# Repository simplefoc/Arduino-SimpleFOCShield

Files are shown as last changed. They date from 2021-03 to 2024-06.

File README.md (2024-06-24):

# Arduino *Simple**FOC**Shield* *v3.2*

  

This is an open-source low-cost Brushless DC (BLDC) motor driver board intended primarily for low-power FOC applications up to 5Amps. The board is fully compatible with the Arduino UNO and all the boards with the standard Arduino headers. The *Simple**FOC**Shield*, in combination with the *Simple**FOC**library* provides user-friendly way to control BLDC motors both in hardware and software. 

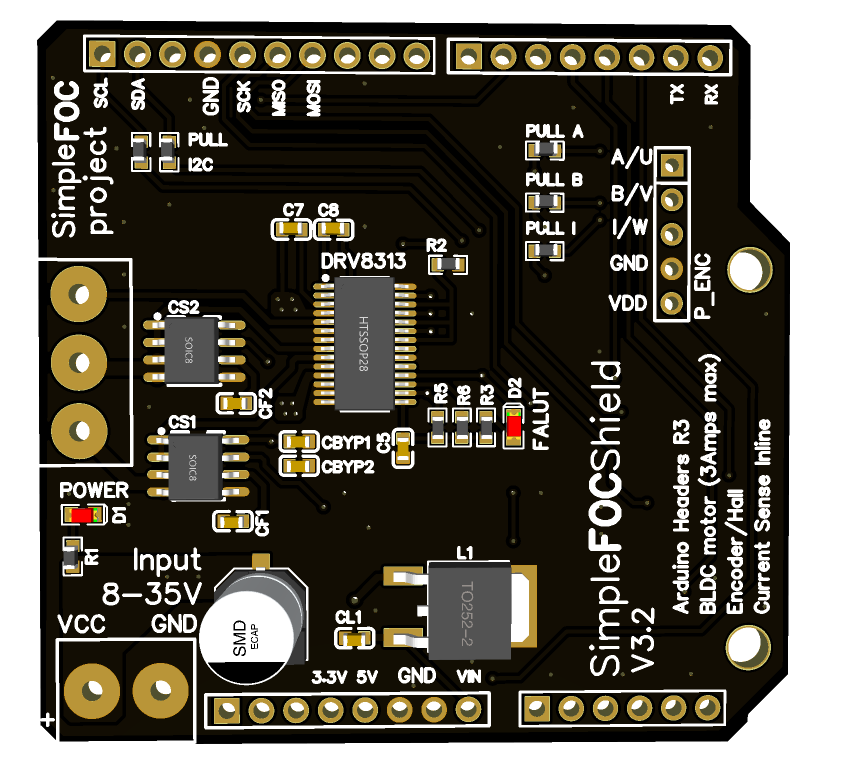
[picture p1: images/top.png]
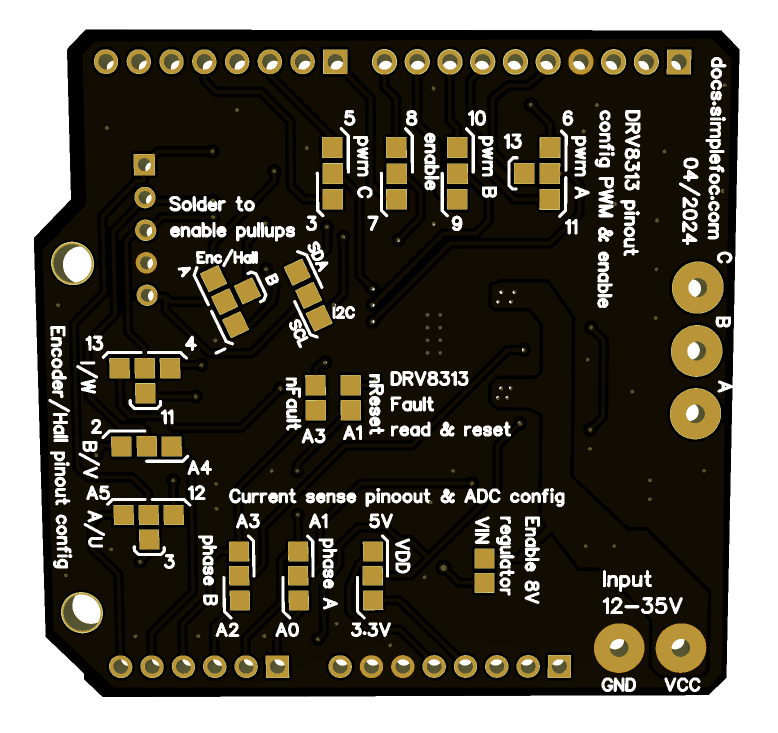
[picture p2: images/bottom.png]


### Features
- **Plug & play**: In combination with Arduino *Simple**FOC**library* - [github](https://github.com/simplefoc/Arduino-FOC)
- **Low-cost**: Price of 15-30€ - [Check the pricing](https://www.simplefoc.com/shop) 
- **In-line current sensing**: Up to 5Amps bidirectional
   - ACS712 hall current sensor
- **Integrated 8V regulator**: 
   - Enable/disable by soldering pads
- **Absolute max ratings** - Designed for Gimbal motors with the internal resistance >10 Ωs. 
   - Max current: 3A, 
   - Max input voltage: 35V
- **Stackable**: running 2 motors in the same time
- **Encoder/Hall sensors interface**: Integrated 3.3kΩ pullups (configurable)
- **I2C interface**: Integrated 4.7kΩ pullups (configurable)
- **Configurable pinout**: Hardware configuration - soldering connections
- **Arduino headers**: Arduino UNO, Arduino MEGA, STM32 Nucleo boards...
- **Open Source**: 
   - Fully designed in **EasyEDA**: [EasyEDA project](https://oshwlab.com/the.skuric/simplefocshield_copy_copy) 🎉
   - Fully available fabrication files - [how to make it yourself](https://docs.simplefoc.com/arduino_simplefoc_shield_fabrication)

### New Features v3.x
 - Transition away from stm's L6234 chip to [DRV8313](https://www.ti.com/lit/ds/symlink/drv8313.pdf?ts=1719079575798), which is much more available
 - Transition form TI's INA240 current amps to Allegro's [ACS712](https://www.sparkfun.com/datasheets/BreakoutBoards/0712.pdf) hall sensors
 - Smaller footprint: 56mm x 53mm
 - Fault and reset pins exposed (optional)
 - Fault led indication
 - Designed completely in EasyEDA, which is a free online PCB design tool - **[Official Easy EDA project](https://oshwlab.com/the.skuric/simplefocshield_copy_copy)**

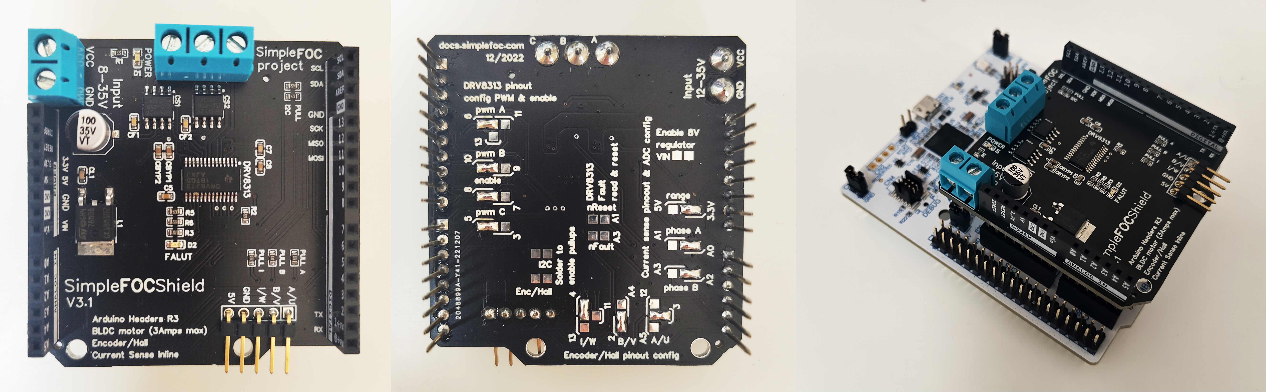
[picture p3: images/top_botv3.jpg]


### Short YouTube demonstration video :D
<p align="">
<a href="https://youtu.be/G5pbo0C6ujE">

</a>
</p>

### Short video guide to fabricating your own *Simple**FOC**Shield* 
<p align="">
<a href="https://youtu.be/sax_9sUgBuk">
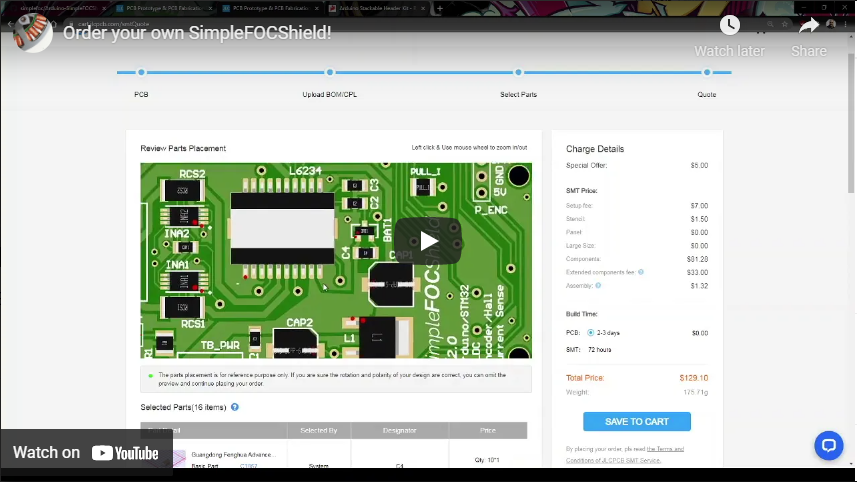
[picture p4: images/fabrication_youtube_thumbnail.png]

</a>
</p>

More info on [board fabrication docs](https://docs.simplefoc.com/arduino_simplefoc_shield_fabrication).

## Board versions:

Feature | <span class="simple">Simple<span class="foc">FOC</span>Shield</span> v1.x | <span class="simple">Simple<span class="foc">FOC</span>Shield</span> v2.x | <span class="simple">Simple<span class="foc">FOC</span>Shield</span> v3.x |
|-|-|-|-|
||||
**PWM Driver** | [L6234](https://www.st.com/resource/en/datasheet/l6234.pdf) | [L6234](https://www.st.com/resource/en/datasheet/l6234.pdf) | [DRV8313](https://www.ti.com/lit/ds/symlink/drv8313.pdf?ts=1719165774986&ref_url=https%253A%252F%252Fwww.google.com%252F)
**Current Sense** | ❌ | [INA240](https://www.ti.com/lit/ds/symlink/ina240.pdf?ts=1719180172738) | [ACS712](https://www.allegromicro.com/en/products/sense/current-sensor-ics/zero-to-fifty-amp-integrated-conductor-sensor-ics/acs712)
**Current measurement range** | ❌ | (configurable) ±3.3/5Amps | ±5Amps
**Onboard LDO** | ❌ | LM7808 | LM7808
**Stackable** | ✔️ | ✔️ | ✔️
**Max current** | 2Amps (5Amp peak) | 2Amps (5Amp peak) | 2Amps (3Amp peak)
**Max voltage** | 24V | 35V | 35V
**Protections** | Overtemperature | Overtemperature | Overtemperature, Overcurrent
**Footprint** | 68mm x 53 mm | 68mm x 53 mm | 56mm x 53mm
**Design tool** | Altium Designer 2019 | Altium Designer 2019 | EasyEDA 

## Release timeline

To check the release timeline, click [here](https://github.com/simplefoc/Arduino-SimpleFOCShield/releases) 

Version  |link | Release date | Comment
----- | ----- | ---- | ----
*Simple**FOC**Shield* v1.3 |[release v1.3](https://github.com/simplefoc/Arduino-SimpleFOCShield/releases/tag/v1.3) | 04/20 | Inital release
*Simple**FOC**Shield* v1.3.1 | [release v1.3.1](https://github.com/simplefoc/Arduino-SimpleFOCShield/releases/tag/v1.3.1) | 07/20 | added Nucleo stacking support
*Simple**FOC**Shield* v1.3.2 |[release v1.3.2](https://github.com/simplefoc/Arduino-SimpleFOCShield/releases/tag/v1.3.2) | 09/20 | added I2C pullups
*Simple**FOC**Shield* v1.3.3 |[release v1.3.3](https://github.com/simplefoc/Arduino-SimpleFOCShield/releases/tag/v1.3.3) | 12/20 | adapted L6234 circuit + full Arduino header
*Simple**FOC**Shield* v2.0 |[release v2.0](https://github.com/simplefoc/Arduino-SimpleFOCShield/releases/tag/v2.0) | 01/21 | - 3A in-line current sensing <br>- 5V regulator <br>- new pinout for hardware config 
*Simple**FOC**Shield* v2.0.1 |[release v2.0.1](https://github.com/simplefoc/Arduino-SimpleFOCShield/releases/tag/v2.0.1) | 01/21 | - reduced via size <br> - configurable range
*Simple**FOC**Shield* v2.0.2 |[release v2.0.2](https://github.com/simplefoc/Arduino-SimpleFOCShield/releases/tag/v2.0.2) | 02/21 | replaced 7805(connected to 5V) with 78M08 (connected to VIN) to be compatible with stm32 Nucleo-64
*Simple**FOC**Shield* v2.0.3 |[release v2.0.3](https://github.com/simplefoc/Arduino-SimpleFOCShield/releases/tag/v2.0.3) | 03/21 | - Shortened the lines from ADC to current sense <br> - Typo fix : underside label switched phase A and phase B
*Simple**FOC**Shield* v2.0.4 |[release v2.0.4](https://github.com/simplefoc/Arduino-SimpleFOCShield/releases/tag/v2.0.4) | 09/21 | - Pullup config simplified <br> - Max input voltage 35V <br> - removed CAP2 for a CL1 <br> - Easy EDA version of the project
*Simple**FOC**Shield* v3.1 |release v3.1 | 10/22 | - Complete redesign <br> - Transition to DRV8313 <br> - Transition to ACS712 <br> - Smaller footprint: 56mm x 53mm<br> - Fault and reset pins exposed (optional) <br> - Fault led indication <br>- Fully developed using EasyEDA
*Simple**FOC**Shield* v3.2 |[release v3.2](https://github.com/simplefoc/Arduino-SimpleFOCShield/releases/tag/v2.0.4) | 04/24 | - Official release <br> - Resolved the bug [#9](https://github.com/simplefoc/Arduino-SimpleFOCShield/issues/9)

## Getting started
You already have your own <span class="simple">Simple<span class="foc">FOC</span>Shield</span>? <br>
[Here is a simple guide how to start preparing your setup](https://docs.simplefoc.com/arduino_simplefoc_shield_installation)

## How to get hold of the *<span class="simple">Simple<span class="foc">FOC</span>Shield</span>*
- **Fabricate the board yourself**:  Please visit the [board fabrication](https://docs.simplefoc.com/arduino_simplefoc_shield_fabrication) to find out how to manufacture the board yourself!<br>
- **Order the finished and tested board**:  Check out our [shop](https://simplefoc.com/simplefoc_shield_product).

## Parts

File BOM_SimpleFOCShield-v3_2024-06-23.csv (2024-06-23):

ID | Name | Designator | Footprint | Quantity | Manufacturer Part | Manufacturer | Supplier | Supplier Part | Price
1 | 470nF | C5 | C0603 | 1 | CC0603ZRY5V6BB474 | YAGEO | LCSC | C327269 | 0.009
2 | 100uF | C6 | CAP-SMD_BD6.3-L6.6-W6.6-FD | 1 | VT1V101M-CRE77 | Vertical Technology | LCSC | C294520 | 0.033
3 | 100nF | C7,C8 | C0603 | 2 | CL10B104KB8NNNC | SAMSUNG | LCSC | C1591 | 0.002
4 | 1uF | CBYP1,CBYP2 | C0603 | 2
5 | 1nF | CF1,CF2 | C0603 | 2
6 | 0.1u | CL1 | C0603 | 1
7 | ACS712ELCTR-05B-T | CS1,CS2 | SOIC-8_L5.0-W4.0-P1.27-LS6.0-BL | 2 | ACS712ELCTR-05B-T | ALLEGRO(美国埃戈罗) | LCSC | C44471 | 1.757
8 | LED-0603_R | D1 | LED0603_RED | 1 | 19-217/R6C-AL1M2VY/3T | EVERLIGHT(台湾亿光) | LCSC | C72044 | 0.018
9 | LED-0603_R | D2 | LED0603_RED | 1 | 19-217/R6C-AL1M2VY/3T | EVERLIGHT(台湾亿光) | Add New Supplier | C72044 | 0.018
10 | DRV8313PWPR | DRV8313 | HTSSOP-28_L9.8-W4.5-P0.65-LS6.6-BL-EP | 1 | DRV8313PWPR | Texas Instruments | LCSC | C92482 | 2.072
11 | L78M08CDT-TR | L1 | TO-252-2_L6.6-W6.1-P4.57-LS9.9-TL-CW | 1 | L78M08CDT-TR | STMicroelectronics | LCSC | C158076 | 0.478
12 | 3.3k | PULL_A1,PULL_I1 | R0603 | 2
13 | 3.3k | PULL_B1 | R0603 | 1 |  |  | LCSC
14 | 4.7k | PULL_SCL,PULL_SDA,R1 | R0603 | 3 | 0603WAF4701T5E | UniOhm | LCSC | C23162 | 0.001
15 | 4.7kΩ | R2,R5,R6 | R0603 | 3 | 0603WAF4701T5E | UniOhm | LCSC | C23162 | 0.001
16 | 330Ω | R3 | R0603 | 1

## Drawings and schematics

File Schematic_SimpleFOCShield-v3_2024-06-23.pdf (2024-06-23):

# ACS712

# Current Sense Circuit

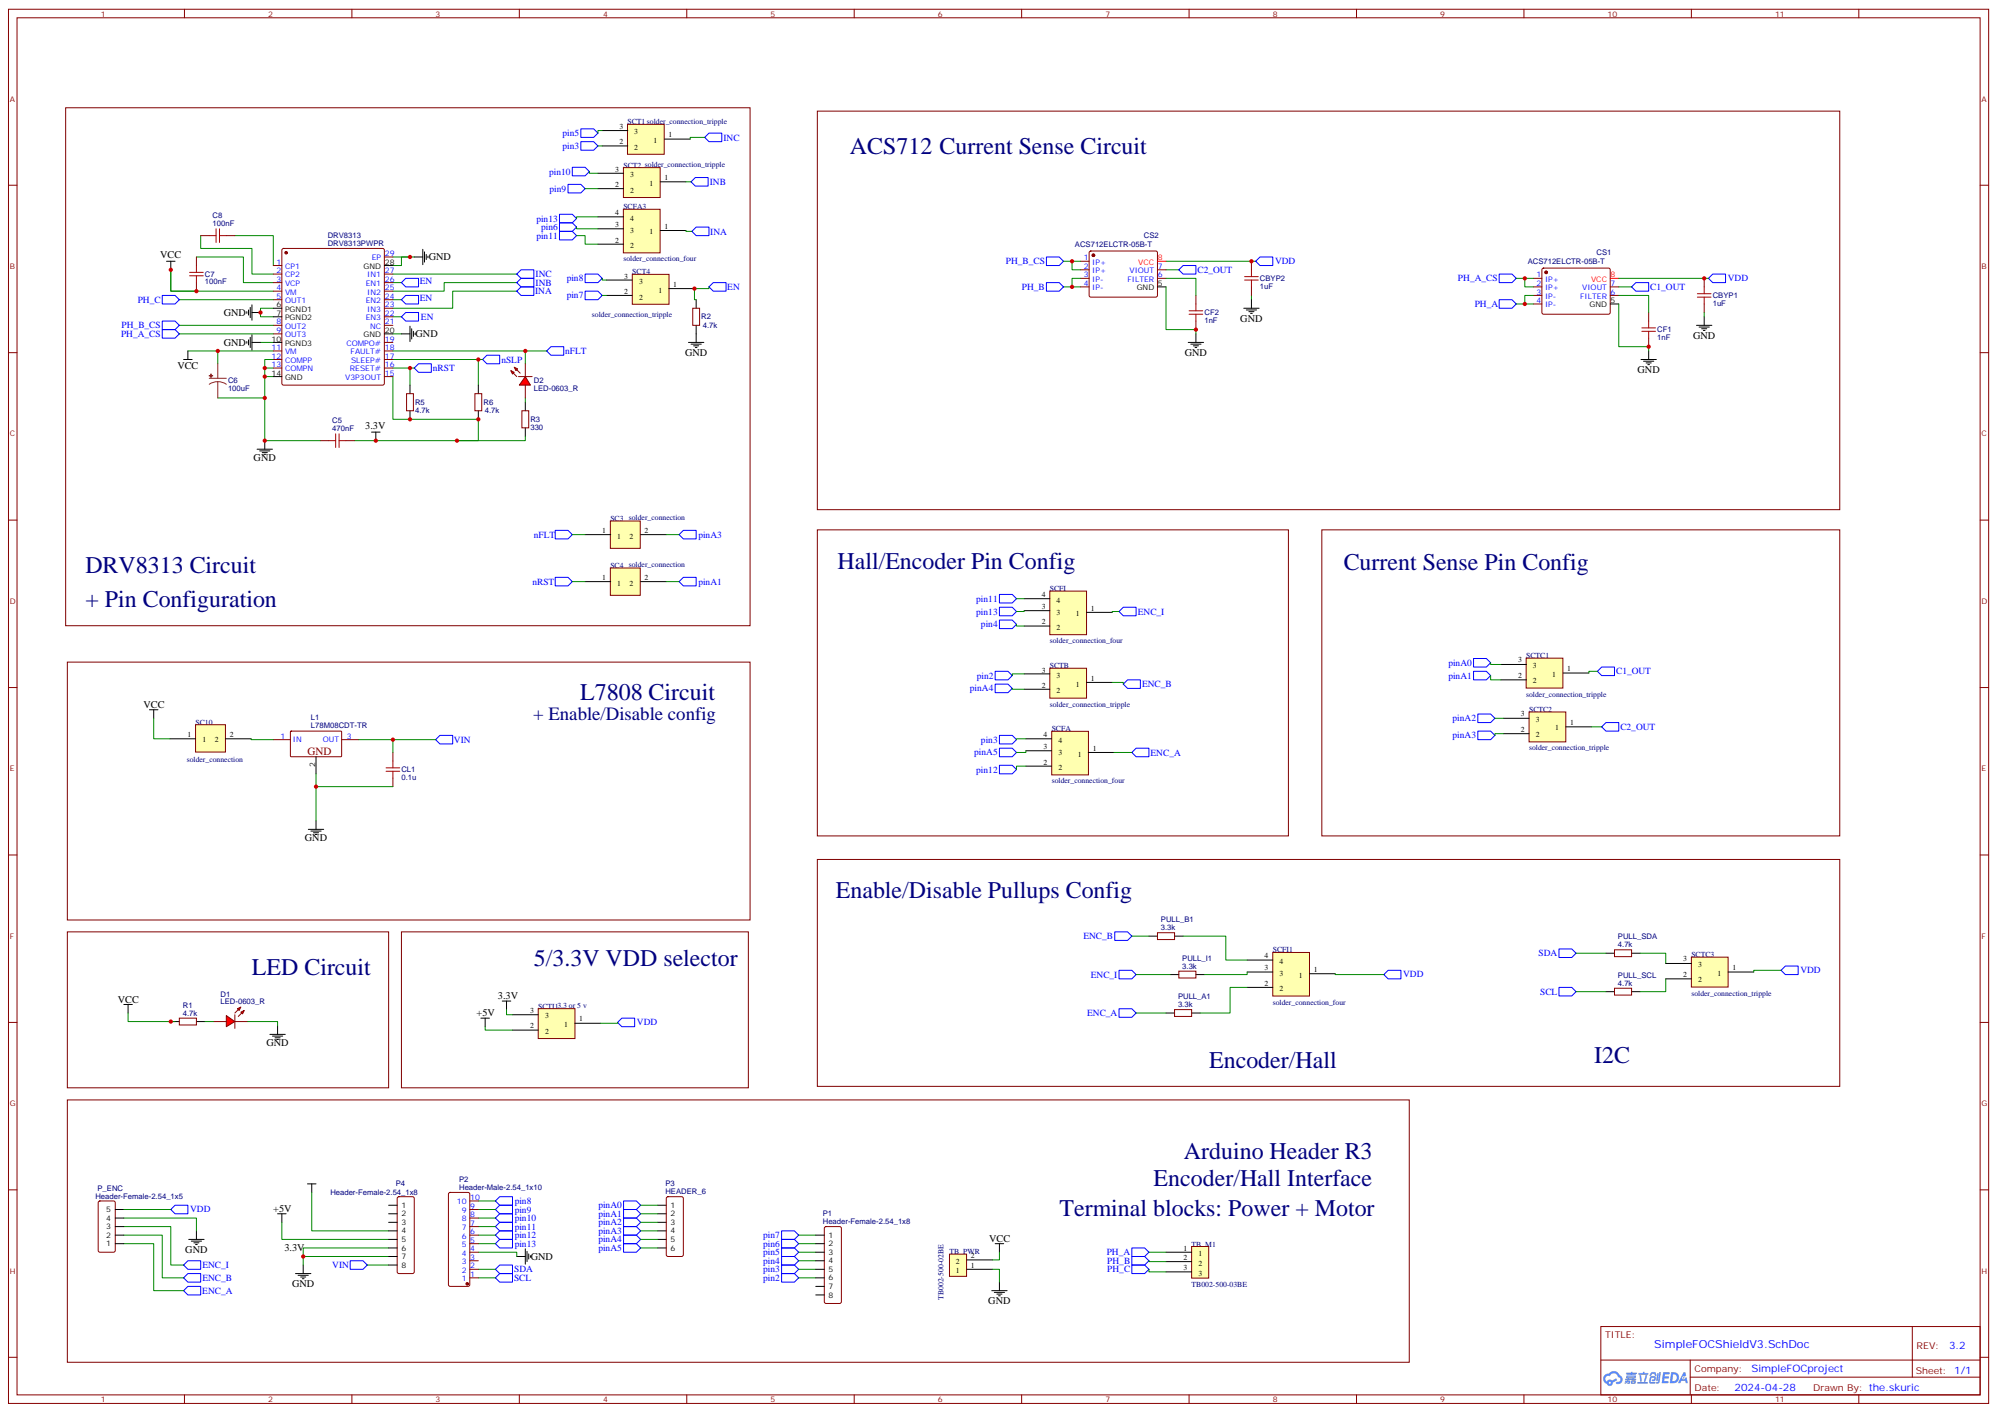
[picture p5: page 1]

Hall/Encoder Pin Config

Current Sense Pin Config

Enable/Disable Pullups Config

Terminal blocks: Power + Motor

Drawn By: the.skuric

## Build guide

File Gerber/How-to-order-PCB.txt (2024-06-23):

How to Order PCB

Please refer to:
https://docs.easyeda.com/en/PCB/Order-PCB

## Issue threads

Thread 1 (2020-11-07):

[Schematic] Diode TBAT45s pin identification error

kingsjl, 2020-11-07:
Schematic diode pin identification error：
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

Correct pin sequence：
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

Closed 2020-11-07.

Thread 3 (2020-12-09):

Arduino SimpleFOCShiled v1.3.3 design error

askuric, 2020-12-09:
Hi guys,

Aaron has just identified a problem with the version of the board v1.3.3.
Check the community forum for more info:
https://community.simplefoc.com/t/motor-makes-loud-noise/316/11

I'll make sure to update the design as soon as possible!

askuric, 2020-12-09:
The v1.3.3 has been fixed to remove the error in [the commit](https://github.com/simplefoc/Arduino-SimpleFOCShield/commit/ead7f148952500506279881f43028458ff9d675f)
The [release v1.3.3](https://github.com/simplefoc/Arduino-SimpleFOCShield/releases/tag/v1.3.3) has been updated to include this bugfix.

Sorry about the inconvenience!

Closed 2021-04-04.

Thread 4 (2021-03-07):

INA240: which gain should be selected for V2.0.2

gowitty, 2021-03-07:
there 4 different gains.  which gain should be selected?
INA240A1 GAIN(V/V) 20
INA240A2 GAIN(V/V) 50
INA240A3 GAIN(V/V) 100
INA240A4 GAIN(V/V) 200

askuric, 2021-03-07:
Hey @gowitty,

So in short, I've taken a choice to use:
- Shunt resistor value: **0.01Ohm**
- Current sense: **INA240A2 (gain 50)**

#### Here is why:

So in general there are two parameters when it comes to current sensing hardware:
 - shunt resistor values
 - amplifier gain

In the case of the *Simple**FOC**Shield*, the BLDC driver chip L6234 has the current limit of 5 Amps. So we need to be able to measure +-5amp current. But in most cases your application with the *Simple**FOC**Shield* will remain in the 3Amp range. Higher currents require appropriate heat evacuation: heat-sinks, fans, etc.

So you need to be able to measure +-3amps for example, which is a 6Amp range.  (or +- 5amps -> 10amp range).
The mcus usually have the 3.3V or 5V logic which tells you that you need the transformation ratiofor example:
```
trans_ratio = 5V / 10amps = 0.5 V/Amp    or    trans_ratio = 3.3V / 10amps = 0.33 V/Amp
```

So now that we know what is the transformation ratio that we need we can proceed to finding the shunt resistor value and the amplification gain. We know that the `trans_ratio = amp_gain*shunt_resistance`. Now there is a trade-off here in between amplification gain and shunt value:
Shunt resistance will be placed in-line with the motor and all the phase current of the motor will pass through the shunt resistor so it is important to choose the value that is the smallest possible value to reduce the heat loss. Additionally by adding the shunt resistors in-line with motors we are actually increasing the phase resistance of the motor, and since we are placing shunt resistors only on two phases this can make the motor unbalanced and this is another reason that makes it really important to keep this value small relatively to the phase resistance of the motor. On the other hand, the smaller the shunt resistor value the smaller the voltage across it that we want to measure. Since the voltage across it is smaller it which makes it more difficult to measure the phase current, because the smaller it is the higher the amplification noise.  So we would prefer to have the shunt resistor value high and amplification gain low to reduce the noise.

Since we know that the phase resistances of the BLDC motors to be used with this board will be in the range of >10Ohm we know that we can take the shunt resistor of >0.01Ohm.
Now we can calculate that for shunt resistor of 0.01 Ohm we would need the amplificaiton gain:
```
amp_gain= 0.5/0.01 = 50     or     amp_gain =  3.3/0.01 = 33
```
So in order to measure the +-5Amps on 5V logic we can use INA240A2 (gain 50)  but on the 3.3V logic that will give us +-3.3Amp range.
If we want to have higer range on 3.3V logic we need to either:
- use INA240A1 (gain 20) which will give us +-8.25Amp range on 3.3V and +-12.5Amp range on 5V.
- use INA250A2 (gain 50) and change the shunt value (ex. 6 miliOhm) which would give use +-5.5Amps range on 3.3V and +-8.5Amps range on 5V

So I've decided to stick with the **0.01Ohm** shunt and **INA240A2** because even +-3.3Amp range is perfectly enough for gimbal motors.

gowitty, 2021-03-13:
Hey @askuric
appreciate sharing so many details!

Closed 2021-03-13.

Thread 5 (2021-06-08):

Header pins too tall?

steph643, 2021-06-08:
On the left, a nucleao-64 with its 8mm pins. On the right, my brand new SimpleFOCShield with its 18.5mm pins, which cannot penetrate fully into the 9mm Arduino header.
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
Is it unintended or am I missing something?

steph643, 2021-08-08:
> I've pivoted from them, for the newest batch though. Even they were out of stock

I'm fighting to find the same kind of connector (in double-row). Would you disclose who your supplier is?

askuric, 2021-08-09:
Hey @steph643,
I've tried many of them and I am buying them online from the webshops as well. Because my quantities are small.

So I've started with the mouser, where I've bought every component separately. But they soon rum out of components.
Then I've bought them from spark fun. But they to run out.
Then Arduino webshop.
The last one I've bought was from afafruit.

And then even the other components disappeared from the market 😃

Closed 2021-06-08.

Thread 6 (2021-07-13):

OneWheel question

vfear, 2021-07-13:
Hello, I am doing a project onewheel, I need a controller with the ability to control the balance.  I have a hoverboard controller with firmware https://github.com/EmanuelFeru/hoverboard-firmware-hack-FOC.  the controller can be controlled via arduino using uart.  can you help me to adapt the balance code with sending to uart.  This is how my project looks like.
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

askuric, 2021-07-20:
Hey @vfear
Very nice project. I have one Onewheel myself and they are relly fun!

I dont think your question has much to do with this repo so I'll transfer it to the balancer repo.

Do you have some kind of IMU or an accelerometer integrated on the board?
Do you use one or two motors for the wheel, in the picture it seems like they are two :D

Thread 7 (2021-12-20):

confuse about pin mux

standback, 2021-12-20:
hi guys.
i have question about  "Customizing pinout",
In the docs.
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
pwmA mapping to pin 9/10
pwmB mapping to pin 3/5

But , according the  note below
`
Now, there is a lot of possible pin configurations and not all of them are possible depending on the microcontroller and sensor you are using. For example, Arduino UNO only has 2 external interrupt pins, and they are pin 2 and 3. Therefore when using the board with Arduino UNO and Encoder we will try to use pin 3 for encoder channel A and not for pwm A.`
it seems mean that  PwmA should  mapping to pin3  instand 9/10.
version2.03 board ,also design that pinA mapping to pin 3/5.
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

is that means  this pinmux(in docs) is  out of date?

I am confused.
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
,
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
which one is right?

askuric, 2021-12-20:
Yeah, it's the docs. It was an example pin out for the earlier version of the board.
Whatever is indicated on the board itself is the right configuration.

We try to keep the docs as up-to-date as possible, but these kinds of stuff are sometimes difficult to detect :)

We'll update it as soon as possible.

standback, 2021-12-20:
Got it,  thanks for your reply.

Closed 2021-12-20.

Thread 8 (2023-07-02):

Increase current limit

kilofeq, 2023-07-02:
Which components I need to change to operate motors with around 10-15A of peak current?

askuric, 2023-07-03:
Hey @kilofeq,

The l6234 driver is not able to drive these kinds of currents.
So you would need a different driver chip, which in most cases is not all in one integrated chip, but would require a set of high and low side mosfets as well as the mosfet driver.
There is no simple way of building on top of the simplefocshiled to achivene thse currents. Its probably easier to start from scratch.

There is a board that might be of interest to you, called [simplefoc-powershield](https://github.com/simplefoc/Arduino-SimpleFOC-PowerShield). with the 30amp current limts, but its performance is relatively limited. Having many issues with the efficiency on higher pwm frequencies.

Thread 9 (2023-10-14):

I2C pullups using ESP32-S2 Metro

wasistdalos, 2023-10-14:
Hi, thank you a lot for the project, the documentation and effort! using the ESP32-S2 Metro there are already I2C pullups included so i didn't connect the jumper on the SimpleFOC V2.0.4. Using that setup with an AS5048b i did run into issues getting I2C communication to work.  Whitout the shield it did work as expected. I solved the issue by desoldering one of the 4,7k I2C pullups of the V2.0.4 shield.  Please check for next shield version, thank you!
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

askuric, 2023-10-14:
Hey @hammerflo,

This is very strange! :thinking:

Did you try to desolder the connection (solder pad) on the bottom side of the board?
There is one:
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

hammerflo, 2023-10-14:
yes i did. looking at the schematic, sda and scl are connected with 2x 4,7k on the shield. maybe this leads to this behaviour?

askuric, 2023-10-14:
Nice catch!
This could be an issue, I did not think about that.
And in that case it make sense that desoldering one of the resistors solved the problem.

I've connected their 5V channel to reduce the number of soldering pads in the v2.0.4. Earlier versions did not have this issue. I'll make sure to separate them in the next release.

askuric, 2024-06-26:
The issue is resolved in the new version of the shield :D

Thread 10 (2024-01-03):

Bad Getting Started link

Candas1, 2024-01-03:
Hi,

It seems the getting started link doesn't work in the readme.
I believe it should be this one:
https://docs.simplefoc.com/arduino_simplefoc_shield_installation

askuric, 2024-06-22:
Thanks I've corrected it!

Closed 2024-06-22.

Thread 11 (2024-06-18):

JLC PCB fabrication instructions no longer work

eduardkieser, 2024-06-18:
I followed the steps described [here](https://www.youtube.com/watch?v=sax_9sUgBuk&t=585s&ab_channel=simplefoc) with version 2.0.4:

but after specifying the bom and pick&place file, I get the following error:
```
File processing failed, please check your file and upload again.
```

I also tried with 2.0 is there an update to the procedure to remain compatible with JLC PCB?

askuric, 2024-06-18:
Hmm, they mush have changed the bom format.
There is probably a different order/naming of columns in the BOM files. The pick and place document should be fine probably.
I'll try to look into it in the next days.

askuric, 2024-06-22:
Hi @eduardkieser,

Thanks for reporting this!
I've just checked and JLCPCB has changed a lot of their requirements for the fabrication files since I've ordered last shields. :D
The new BOM and CPL files are in available in the repo.

You might have to hurry up because there are just 24 L6234 available in the jlcpcb parts as of today (22/06/2024) :D

eduardkieser, 2024-06-22:
@askuric Thanks so much!
Will take a look as soon as I get a moment.

eduardkieser, 2024-06-27:
Tested last night. Works beautifully, thanks! closing.

Closed 2024-06-27.

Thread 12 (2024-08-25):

Charge pump capacitor out of spec

NoraS022, 2024-08-25:
According to the DRV8313PWPR documentation CPL and CPH should have a 0.01μF ceramic capacitor not a 0.1μF as in the schematic. It may not matter since the board obviously does work, I just don't know enough about charge pumps for FETs to determine that but it may have two different capacitors for a reason.

"Because the output stages use N-channel FETs, the device requires a gate-drive voltage higher than the VM
 power supply to enhance the high-side FETs fully. The DRV8313 integrates a charge-pump circuit that generates
 a voltage above the VM supply for this purpose.
 The charge pump requires two external capacitors for operation. See the block diagram and pin descriptions for
 details on these capacitors (value, connection, and so forth)."

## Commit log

2020-09-21 v1.3 upload
    [ArduinoFOC.GBL, ArduinoFOC.GBO, ArduinoFOC.GBP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]
2020-09-21 v1.3.1 upload
    [ArduinoFOC.GBL, ArduinoFOC.GBO, ArduinoFOC.GBP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]
2020-09-21 v1.3.2 upload
    [ArduinoFOC.GBL, ArduinoFOC.GBO, ArduinoFOC.GBP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]
2020-10-07 FIX updated the pick and place files
    [Pick Place for ArduinoFOC.csv]
2020-10-07 README added i2c pullups
2020-11-07 version 1.3.3
    [ArduinoFOC.GBL, ArduinoFOC.GBO, ArduinoFOC.GBP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]
2020-12-09 v1.3.3 bugfix ground plane + altium model of v1.3.3
    [ArduinoFOC.GBL, ArduinoFOC.GBO, ArduinoFOC.GBP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]
2020-12-09 pick and place rotation update
    [Pick Place for ArduinoFOC.csv]
2020-12-09 fix bat56 rotation
    [Pick Place for ArduinoFOC.csv]
2021-01-09 version 2.0
    [ArduinoFOC.GBL, ArduinoFOC.GBO, ArduinoFOC.GBP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]
2021-01-13 version 2.0.1
    [ArduinoFOC.GBL, ArduinoFOC.GBO, ArduinoFOC.GBP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]
2021-01-14 version v2.0.2 changed regulator to 7808
    [BOM.xlsx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]
2021-03-07 version v2.0.3
    [BOM.xlsx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]
2021-07-18 v2.0.4 inital commit
    [ArduinoFOC.GBL, ArduinoFOC.GBO, ArduinoFOC.GBP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]
2024-06-22 added the updated bom and pick and place bugfix #11
    [BOM.xlsx, Pick Place for ArduinoFOC.csv]
2024-06-23 new version of the shield
    [ArduinoFOC.GBL, ArduinoFOC.GBO, ArduinoFOC.GBP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]

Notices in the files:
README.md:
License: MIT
